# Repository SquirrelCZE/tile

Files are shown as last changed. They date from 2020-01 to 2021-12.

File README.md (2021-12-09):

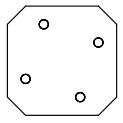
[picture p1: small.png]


# Tile

Tile is a generic mounting system designed for small robots. 
It is a specification of dimensions of one mount position with positions of four screws.
The idea is that one can attach anything to said position, from 3D printed parts to PCBs.

This gives as abillity to easily reuse parts and rebuild the robot in different configuration easily, same way one could expect from LEGO.
The key difference is that it is more sturdy (as screws are used) and it is easy to make compatible PCB.

We intentially designed the tile to allow mounting of parts on thin wall from both sides.
This is achieved by shifting the holes in a way, that when the shape is flipped, the holes won't collide (even when one uses nuts to screw something in place)

The position is shaped like square with beveled corners, this makes it possible to form a grid of mount positions. 
Bigger parts can overlap multiple tiles, it is up to designed to decided whenever that is sensible choice.
Corners are beveled to create a spot between positions on grid for wires.

Given that we use this for 3D printing, the models expect nuts to be inserted in the models to get proper screw thread.

The most used configuration T24 is 24x24mm square with four positions for M2 screws.

The tile is used in our robot Koke heavily https://schpin.org/robots/koke.html and we allready benefited from this on another robot that just reused a lot of the parts.

## Repository content

The main truth for the tile is it's SCAD library - `tile.scad`.
The rest of the repository is as follows:

 * **dxf/** contains dxf shapes for some grid layous that can be directly imported to other CADs made with SCAD. Note that SCAD approximates circles with n-gon.	
 * **example/** simple examples of tile shapes that can be used
 * **extra/** contains more complex models using tile, such as holder for raspberry or 90degree bracket.
 * **pcb/** PCBs used for our robot designed in KiCAD that are Tile compatible.

## Gallery

### Examples

Simple square with T24 mount on both sides:

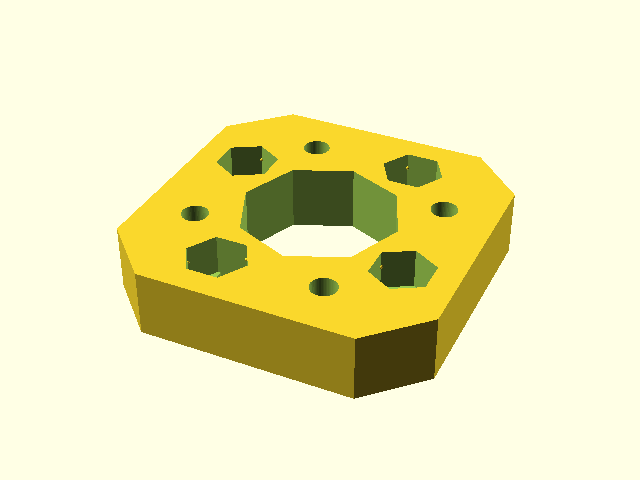
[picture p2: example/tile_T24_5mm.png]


### Koke

This is an example of more complex assembly: part of Koke's leg.
You can see that the parts are connected with tiles (such as the tip of the leg) and that there are multiple tile mount spots.

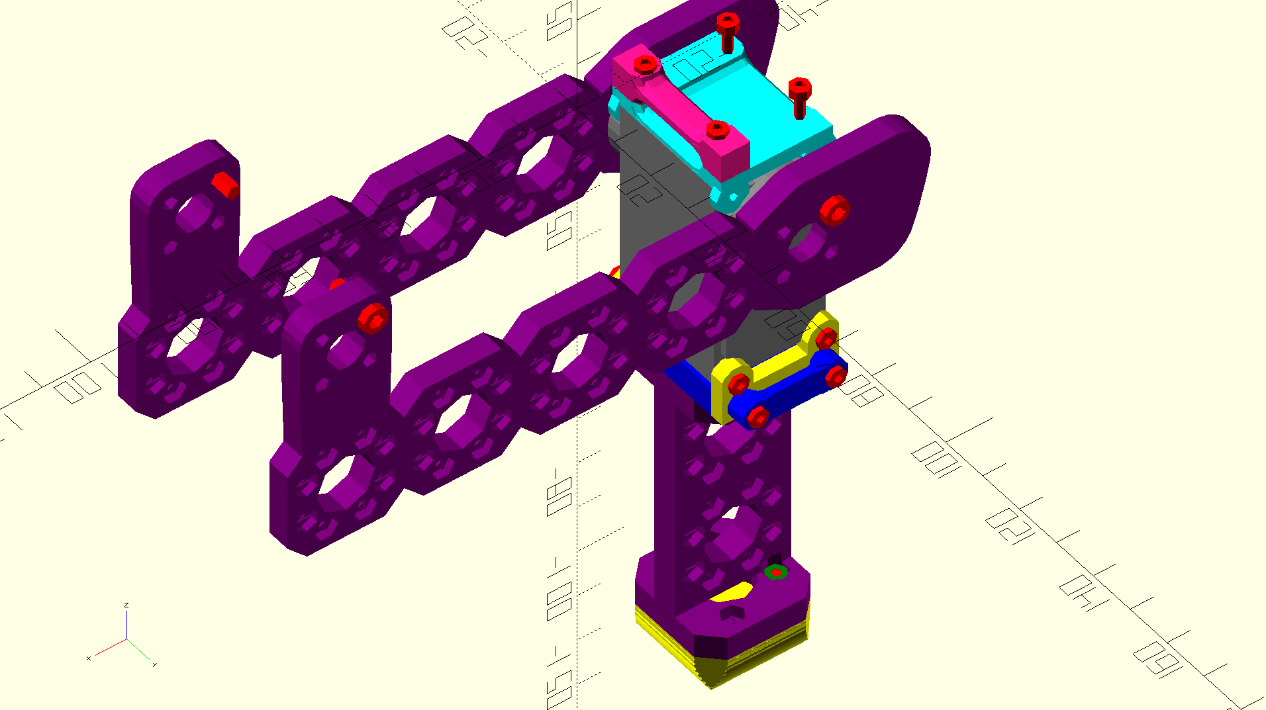
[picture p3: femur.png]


### PCBs

There are two PCBs that are in production stage (that is they may be improved in time but there is little motivation to do so). 
Both are designed in KiCAD and we buy them in bulk.

The first one is small 4-layer power distribution board for use with our servomotors.
The power is brought in usually via the XT30 connector space and we have multiple of these on the robot itself.
We have custom footprint for servoconnectors that is compatible with servomotor connectors with 2.54/2mm spacing with pins in following configuration: S|VCC|GND. 
The idea is that servomotors are connected to free servo connectors and one is left to connect the S| |GND pair to the controller (that is, without the VCC line).

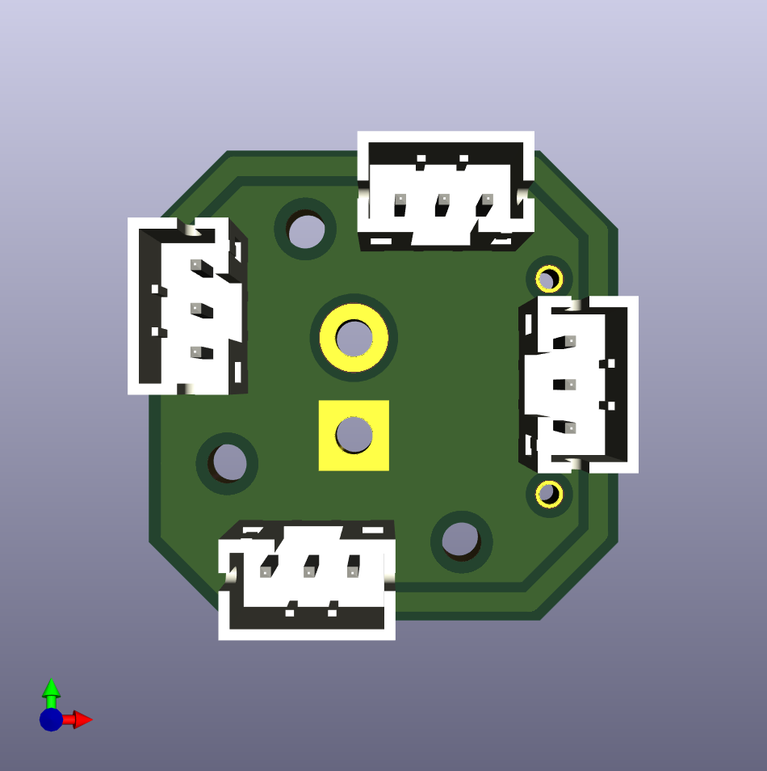
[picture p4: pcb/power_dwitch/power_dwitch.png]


Second board is just really simple holder for two housings for 18650 batteries, that are pararelly connected. 
There are no connectros to be used, rather we expect the wires to be soldered directly on the board itself.

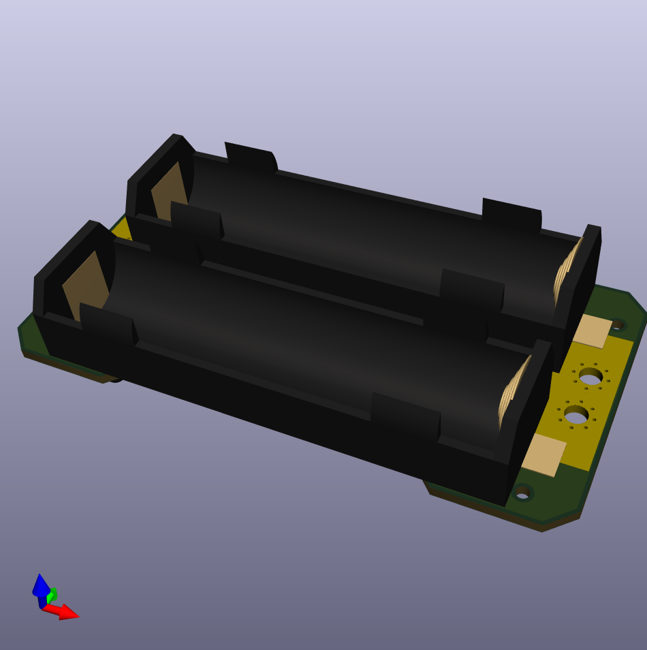
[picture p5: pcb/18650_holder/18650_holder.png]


### Prototype PCBs

We have a prototype of board with STM32G4 processor that can be powered from PDB board above.
The board is designed to control our servomotors or to be attached to same communication bus.

The v1 prototype worked (as we could write code for it and blink a LED), but it misses logic level shifter for the servo bus which makes it not really usable.

The v2 fixes that and even adds IMU, however we should switch to smaller package for the processor to fit all on one side of the PCB and we can't do that now given chip shortage, so v2 is delayed until we can do that.

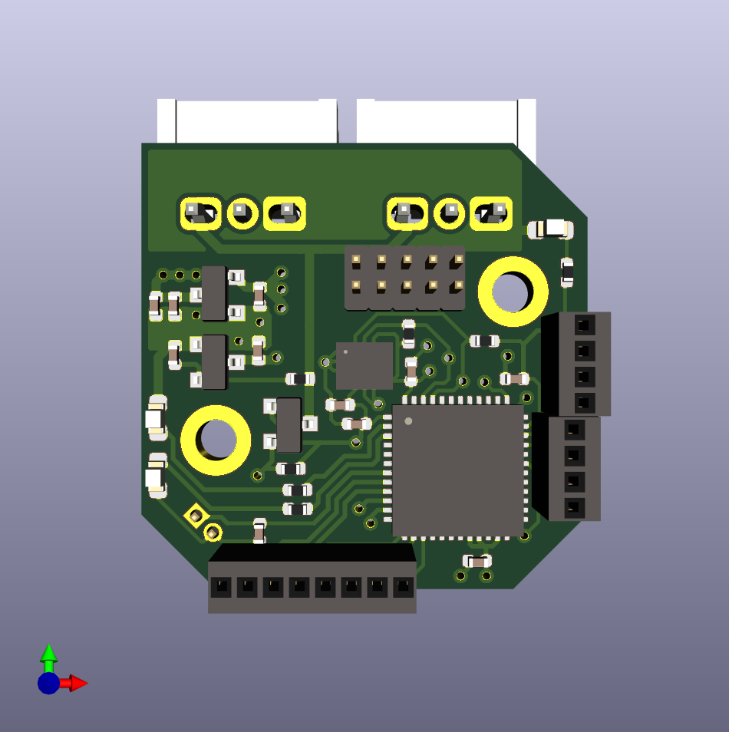
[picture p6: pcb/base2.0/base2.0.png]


## Drawings of T24

All dimensions are in `mm`.

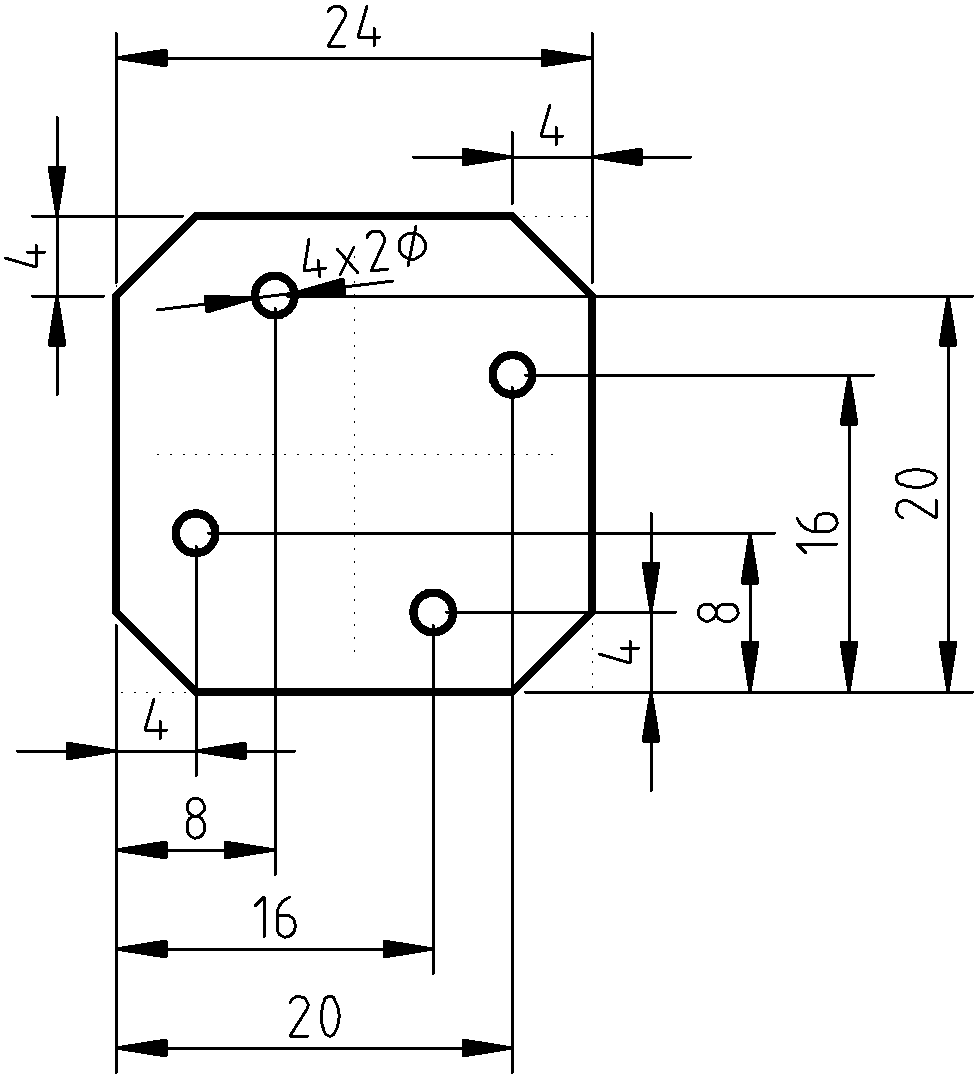
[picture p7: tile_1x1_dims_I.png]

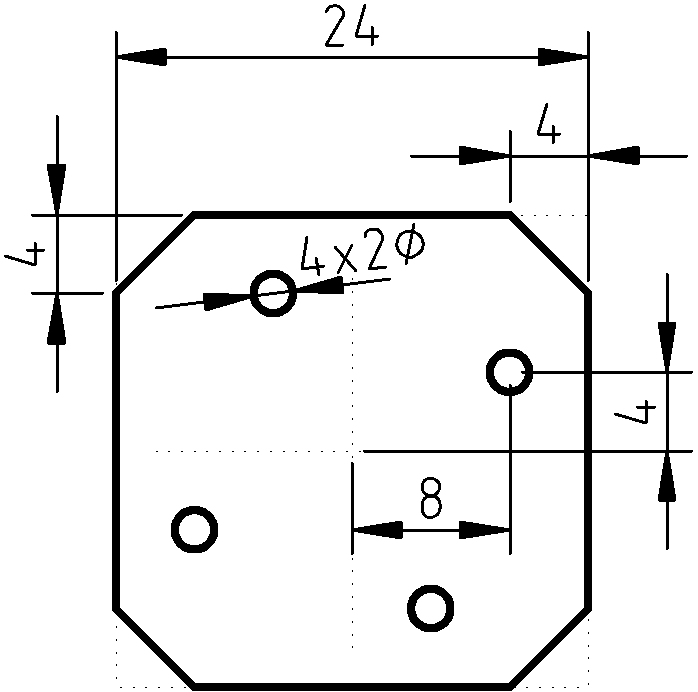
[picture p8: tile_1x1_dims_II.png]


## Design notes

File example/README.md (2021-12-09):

# Gallery of tile examples
## example/tile_T24_5mm_centered.scad
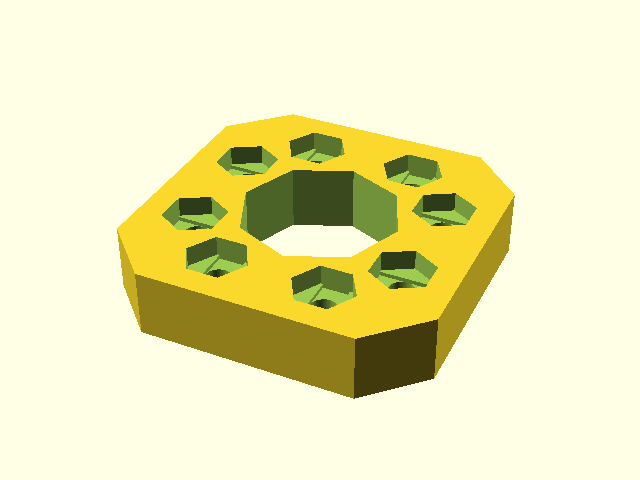
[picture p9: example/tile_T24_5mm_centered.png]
example/tile_T24_5mm_centered

## example/tile_H_T24_5mm.scad
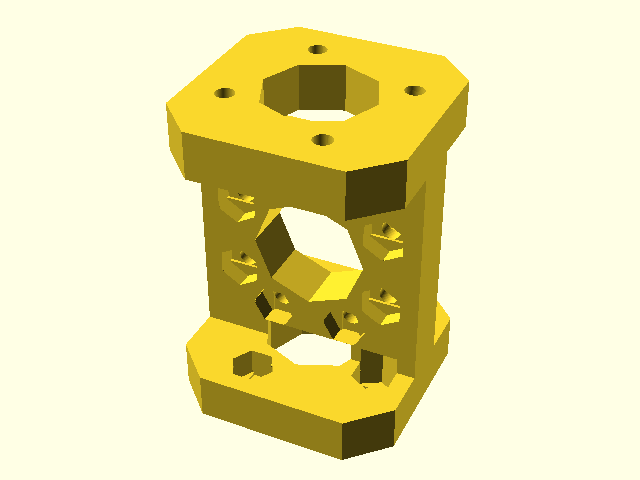
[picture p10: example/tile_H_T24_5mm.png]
example/tile_H_T24_5mm

## example/tile_sandwitch.scad
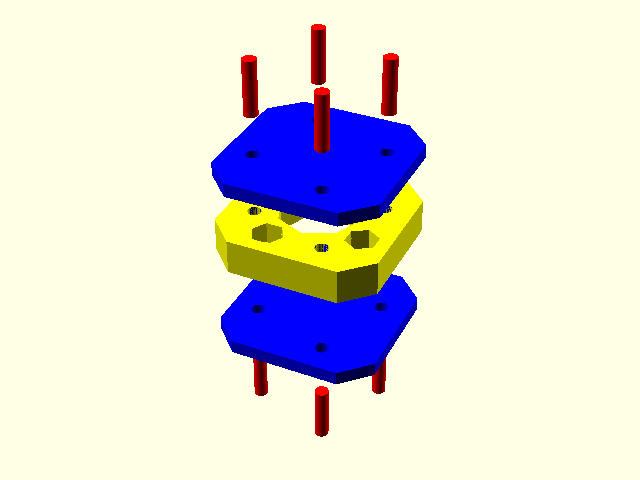
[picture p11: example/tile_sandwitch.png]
example/tile_sandwitch

## example/tile_T24_2mm.scad
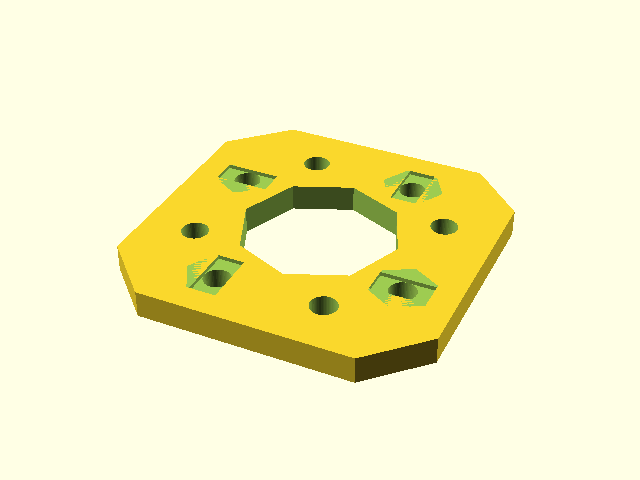
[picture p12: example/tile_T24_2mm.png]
example/tile_T24_2mm

## example/tile_raw_plate_T24_2x3_2mm.scad
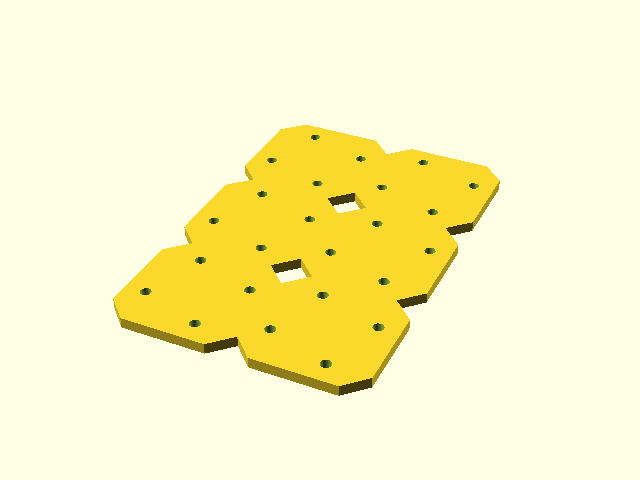
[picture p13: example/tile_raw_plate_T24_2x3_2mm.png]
example/tile_raw_plate_T24_2x3_2mm

## example/tile_T36_5mm.scad
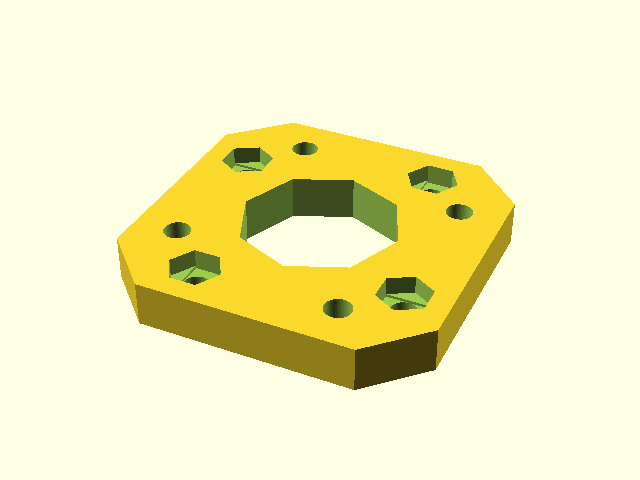
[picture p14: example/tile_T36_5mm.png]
example/tile_T36_5mm

## example/tile_T24_5mm.scad
example/tile_T24_5mm

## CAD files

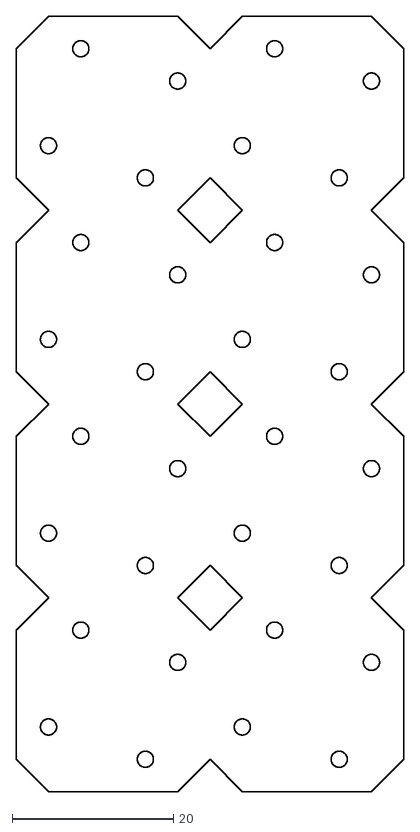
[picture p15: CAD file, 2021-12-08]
dxf/tile_2x4.dxf
48.0 x 96.0

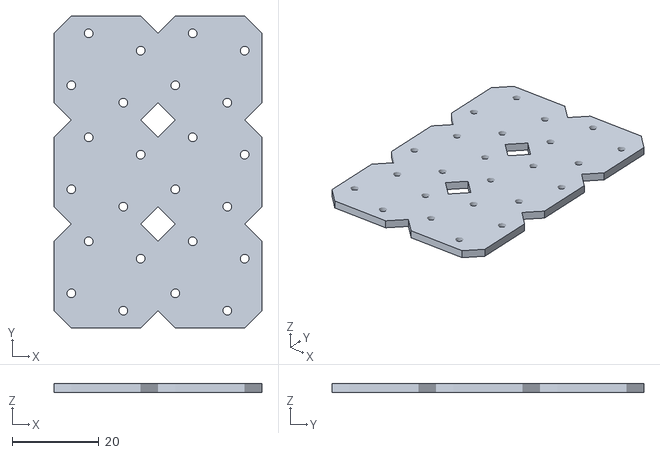
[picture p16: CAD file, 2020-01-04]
example/tile_raw_plate_T24_2x3_2mm.stl
48.0 x 72.0 x 2.00

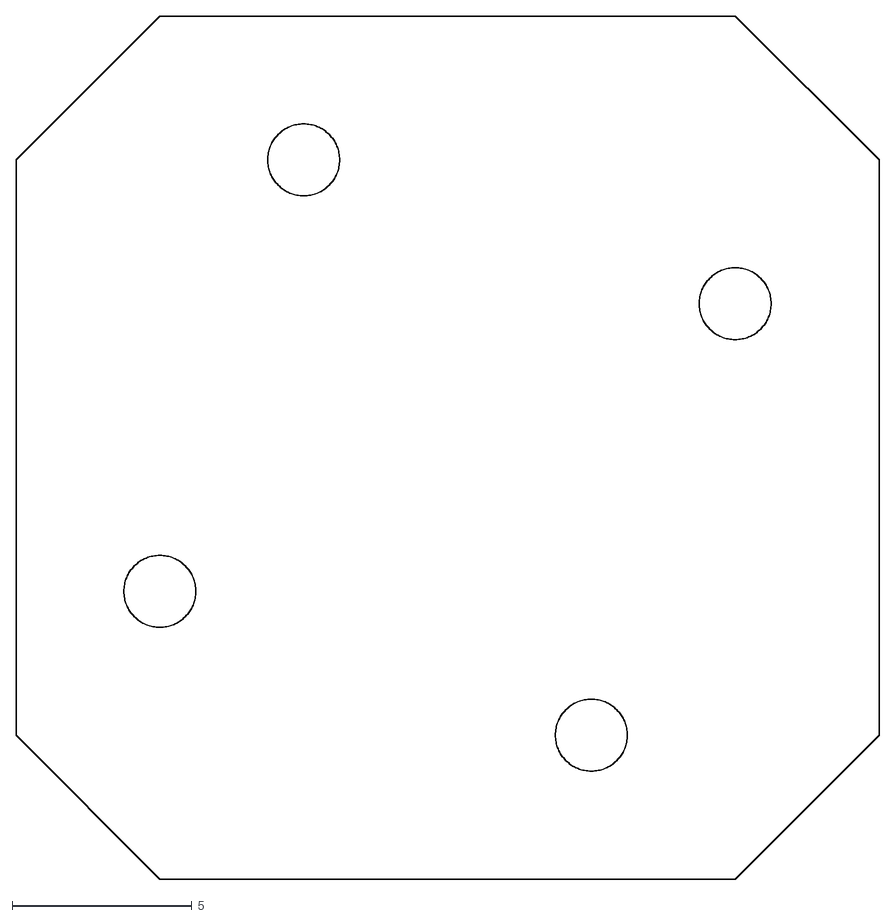
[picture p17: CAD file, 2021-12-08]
dxf/tile_1x1.dxf
24.0 x 24.0

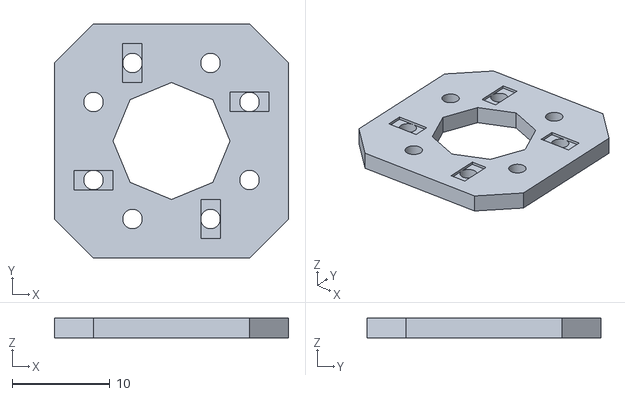
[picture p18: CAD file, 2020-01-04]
example/tile_T24_2mm.stl
24.0 x 24.0 x 2.00

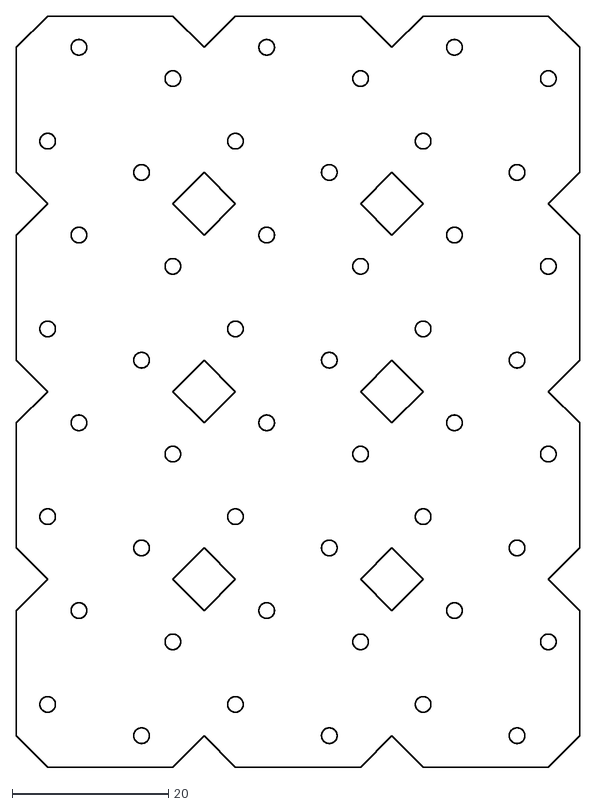
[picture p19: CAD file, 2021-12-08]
dxf/tile_3x4.dxf
72.0 x 96.0

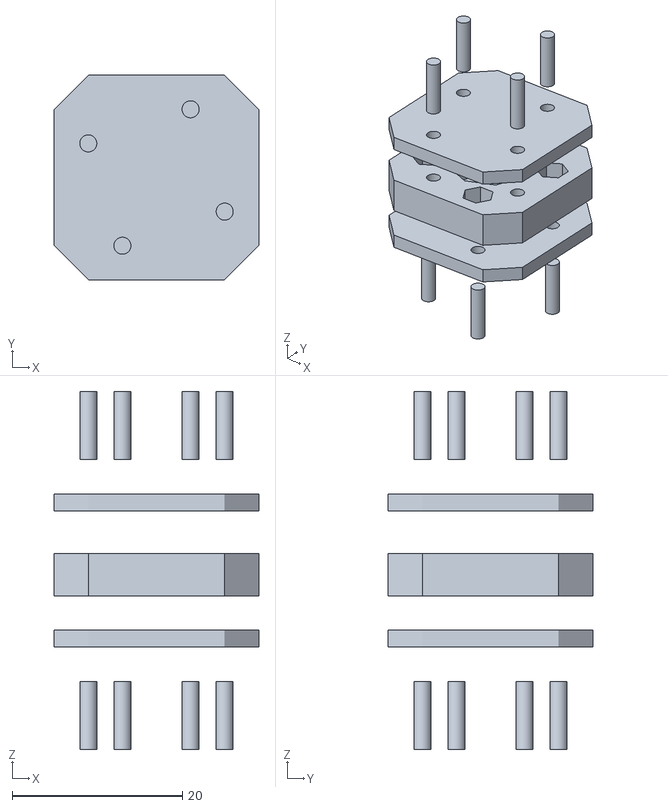
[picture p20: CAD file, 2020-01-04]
example/tile_sandwitch.stl
24.0 x 24.0 x 42.0

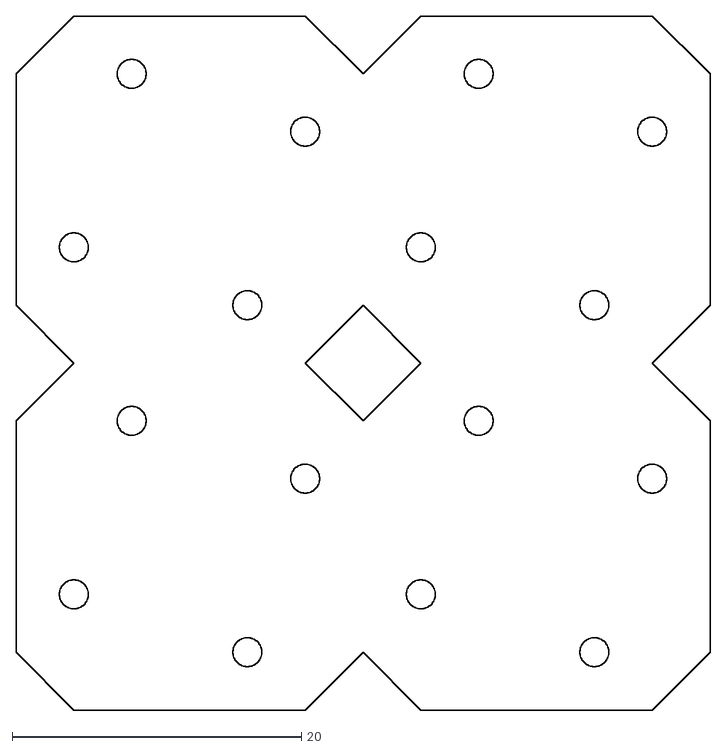
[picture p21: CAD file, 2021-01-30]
dxf/tile_2x2.dxf
48.0 x 48.0

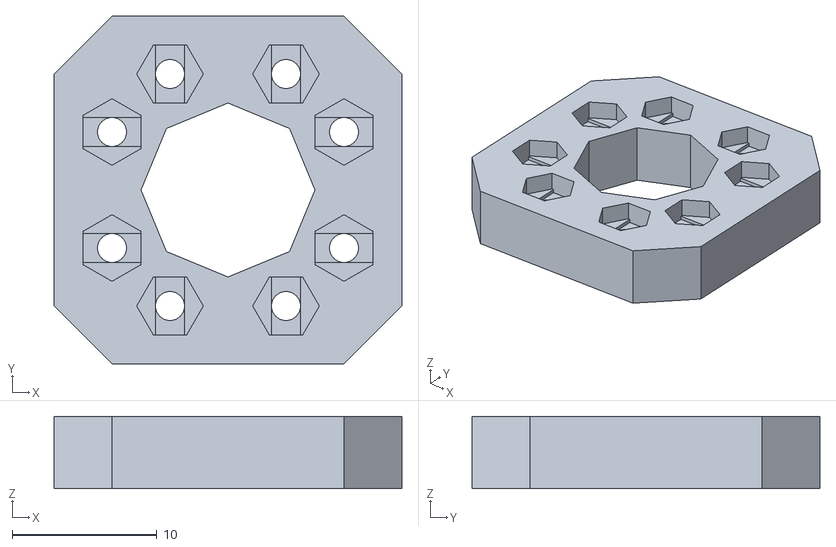
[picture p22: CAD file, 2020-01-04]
example/tile_T24_5mm_centered.stl
24.0 x 24.0 x 5.00

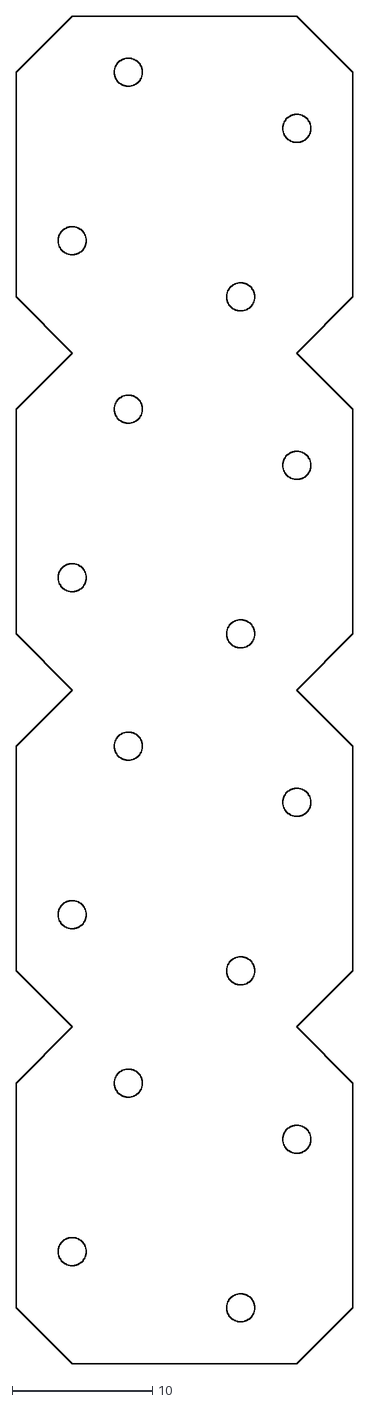
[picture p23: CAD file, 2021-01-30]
dxf/tile_1x4.dxf
24.0 x 96.0

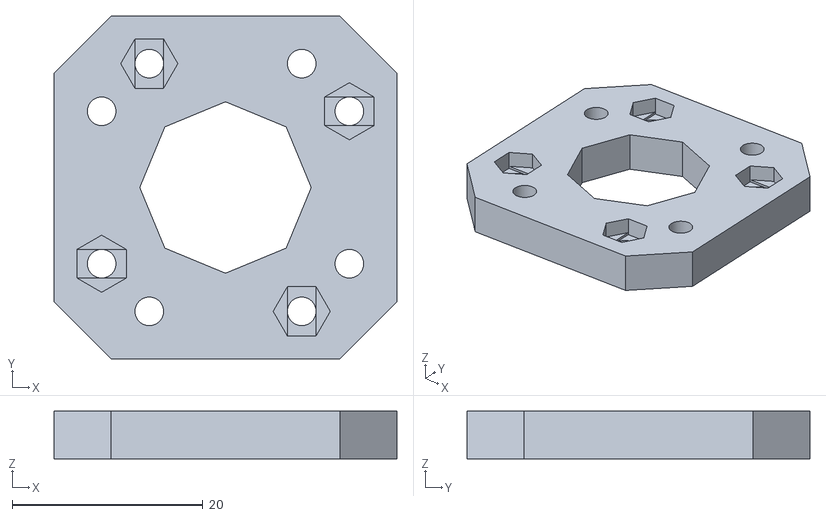
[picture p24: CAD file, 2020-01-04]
example/tile_T36_5mm.stl
36.0 x 36.0 x 5.00

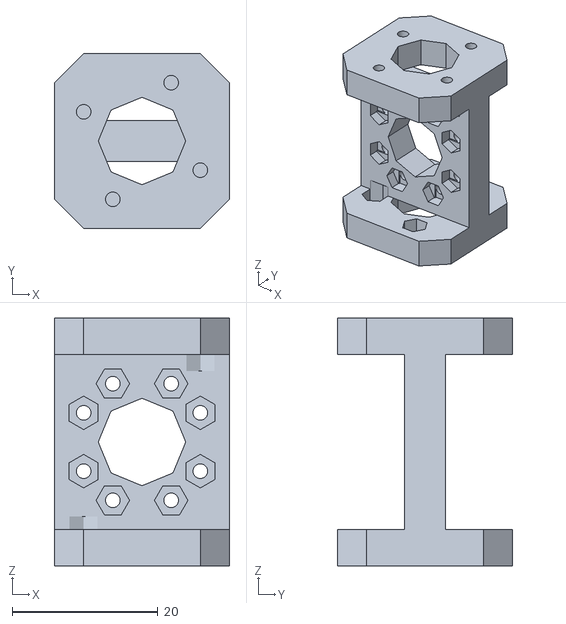
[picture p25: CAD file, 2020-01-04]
example/tile_H_T24_5mm.stl
24.0 x 24.0 x 34.0

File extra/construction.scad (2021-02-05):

include<../tile.scad>;

t = 2;

$fn = 64;
// for (i = [ -1, 0, 1 ]) translate([ i * Ta(T24), 0, 0 ]) tile(T24, 4);

module bracket_base() difference() {
  union() {
    for (rot = [ [ 0, 90, 0 ], [ 180, 0, 0 ] ])
      rotate(rot) translate([ Ta(T24) / 2, 0, 0 ]) tile_raw_plate(T24, 1, 1, 4);
  }

  for (rot = [ [ 0, 90, 0 ], [ 180, 0, 0 ] ])
    rotate(rot) translate([ Ta(T24) / 2, 0, 0 ]) {
      tile_center_hole(T24, h = 100, center = true);
      tile_screw_pos(T24){
	  cylinder(d = Tscrew_d(T24), h = 100, center = true);
		translate([0,0,t])
		cylinder(d= Tnut_d(T24), h=Ta(T24)/2 - t, $fn=6);
		}
    }
}

module bracket_support(i) {
  hull() intersection() {
    bracket_base();
    translate([ 0, i * Ta(T24), 0 ]) cube([ 100, t, 100 ], center = true);
  }
}

module bracket() {
  bracket_base();
  for (i = [ -0.5, 0.5 ]) difference() {
      bracket_support(i);
      scale([ 0.7, 1, 0.7 ]) bracket_support(i);
    }
}

bracket();

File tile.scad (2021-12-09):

//      0   1             2         3  4      5      6
//    [ a,  screw_coord,  corner_r, t, nut_d, nut_h, screw_d]
T36 = [ 36, [ 13, 8, 0 ], 6.000000, 3, 6.000, 2.500, 3 ];
T24 = [ 24, [ 08, 4, 0 ], 4.000000, 2, 4.750, 1.800, 2 ];

tile_k = 0.07;

function Ta(class) = class[0];
function Tscrew_coord(class) = class[1];
function Tcorner(class) = class[2];
function Tt(class) = class[3];
function Tnut_d(class) = class[4];
function Tnut_h(class) = class[5];
function Tscrew_d(class) = class[6];

module tile(class = T24, h = 5, center = false, centered_hole = false) difference() {
	tile_pos(class = class, h = h, center = center);
	tile_neg(class = class, h = h, center = center,
		 centered_hole = centered_hole);
}

module tile_neg(class, h, center = false, centered_hole = false) {
	translate([ 0, 0, center ? 0 : h / 2 ]) for (alpha = [ 0, 180 ])
	    rotate([ alpha, 0, 0 ]) tile_screw_pos(class = class)
		tile_screw_hole(class = class, h = h,
				centered_hole = centered_hole);
	tile_center_hole(class, h + 2, center = center);
}

module tile_pos(class, h, center = false)
    linear_extrude(height = h, center = center, convexity = 10)
	tile_relief(class = class);

module tile_H(class = T24, h = 5, n = 1, center_t = undef) render()
    difference() {
	top_offset = n * Ta(class) + h;
	z_center = n * Ta(class) / 2 + h;
	center_t =
	    (center_t == undef) ? Tt(class) + 2 * Tnut_h(class) : center_t;

	union() {
		translate([ 0, 0, z_center ])
		    cube([ Ta(class), center_t, n * Ta(class) + 2 * h ],
			 center = true);
		for (z = [ 0, top_offset ])
			translate([ 0, 0, z ]) linear_extrude(height = h)
			    tile_base_shape(l = Ta(class),
					    corner_r = Tcorner(class));
	}

	for (i = [0.5:n])
		translate([ 0, 0, h + i * Ta(class) ]) rotate([ 90, 0, 0 ]) {
			tile_neg(class, h = center_t, center = true,
				 centered_hole = true);
			tile_center_hole(class, h = center_t, center = true);
		}

	for (z = [ 0, top_offset ])
		translate([ 0, 0, z ]) tile_center_hole(class, h = h);

  mirror([0,0,1])
      mirror([ 1, 0, 0 ]) tile_screw_pos(class = class)
	    translate([ 0, 0, -h / 2 ]) tile_screw_hole(class = class, h = h);

	tile_screw_pos(class = class)
	    translate([ 0, 0, top_offset + Tt(class) ])
		tile_screw_hole(class = class, h = h);
}

module tile_box_side_pos() {
	children();
	for (alpha = [0:90:360]) rotate([ 90, 0, alpha ]) children();
	rotate([ 180, 0, 0 ]) children();
}

module tile_box(class) difference() {
	hull() {
		r = Tt(class);
		cube([ Ta(class) - r, Ta(class) - r, Ta(class) ],
		     center = true);
		cube([ Ta(class), Ta(class) - r, Ta(class) - r ],
		     center = true);
		cube([ Ta(class) - r, Ta(class), Ta(class) - r ],
		     center = true);
	}

	tile_box_side_pos() cylinder(d = Ta(class) / 2, h = Ta(class));

	tile_box_side_pos() tile_screw_pos(class = class)
	    translate([ 0, 0, Ta(class) / 2 - Tnut_h(class) - 1.5 * Tt(class) ])
		Mnut_sidehole(M2N, 10);
	tile_box_side_pos() tile_screw_pos(class = class)
	    cylinder(d = Tscrew_d(class), h = 20);
}

module tile_raw_plate(class, x, y, t) {
	for (i = [0:x - 1])
		for (j = [0:y - 1])
			translate([ i * Ta(class), j * Ta(class), 0 ])
			    difference() {
				tile_pos(class, h = t, center = false);
				tile_screw_pos(class = class)
				    cylinder(d = Tscrew_d(class), h = 100,
					     center = true);
			}
}

//          Implementation
// ------------------------------------

module tile_center_hole(class, h, center = false) {
  translate([ 0, 0, - tile_k ])
	  cylinder(d = Ta(class) / 2, h = h + 2, center = center, $fn = 8);
}

module tile_base_shape(l, corner_r) {
	hull() {
		square([ l - corner_r * 2, l ], center = true);
		square([ l, l - corner_r * 2 ], center = true);
	}
}

module tile_relief(class, a, corner_r, t, nut_d) {
	tile_base_shape(Ta(class), Tcorner(class));
}

module tile_screw_pos(class) {
	for (alpha = [0:90:360])
		rotate([ 0, 0, alpha ]) translate(Tscrew_coord(class))
		    children();
}

module tile_plate(class, t) difference() {
	linear_extrude(height = t) tile_base_shape(Ta(class), Tcorner(class));

	mirror([ 1, 0, 0 ]) tile_screw_pos(class)
	    cylinder(d = Tscrew_d(class), h = t * 3, center = true);
}

module tile_screw_hole(class, h, centered_hole = false) {
	layer_t = 0.3;
	nut_e = sqrt(pow(Tnut_d(class), 2) - pow(Tnut_d(class) / 2, 2));

	cylinder(d = Tscrew_d(class), h = h + 2, center = true);
	if (centered_hole) {
		for (alpha = [ 0, 180 ])
			rotate([ alpha, 0, 0 ])
			translate([ 0, 0, Tt(class) / 2 ])
				difference() {
					union(){
						cube([ nut_e, Tscrew_d(class), layer_t * 2 ],
				     	center = true);
						rotate([ 0, 0, 30 ])
				    	cylinder(d = Tnut_d(class), h = h, $fn = 6);
					}
					tile_screw_clips(class);
				}
	} else {
		rotate([180,0,0])
		translate([ 0, 0, Tt(class) - h / 2 ]) difference() {
			union() {
				cube([ nut_e, Tscrew_d(class), layer_t * 2 ],
				     center = true);
				rotate([ 0, 0, 30 ])
					cylinder(
				    d = Tnut_d(class),
			  		h = h - Tt(class) + Tnut_h(class), $fn = 6);
			}
			tile_screw_clips(class);
		}
	}
}

module tile_screw_clips(class) {
	for(an=[0, 120, -120])
		rotate([0,0,an+30])
		translate([Tnut_d(class)/2, 0, Tnut_h(class)])
			sphere(r=Tnut_d(class)*0.03);
}

module tile_tube_hole(d) {
	rotate([ 90, 0, 0 ]) cylinder(d = d, h = 100, center = true);
}

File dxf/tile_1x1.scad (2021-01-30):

include <../tile.scad>

projection()
tile_raw_plate(T24, 1, 1, 2);

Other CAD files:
example/tile_T24_5mm.stl
dxf/tile_1x4.scad
dxf/tile_2x2.scad
dxf/tile_2x4.scad
dxf/tile_3x4.scad
example/tile_H_T24_5mm.scad
example/tile_T24_2mm.scad
example/tile_T24_5mm.scad
example/tile_T24_5mm_centered.scad
example/tile_T36_5mm.scad
example/tile_raw_plate_T24_2x3_2mm.scad
example/tile_sandwitch.scad
extra/realsense.scad
extra/rpi.scad

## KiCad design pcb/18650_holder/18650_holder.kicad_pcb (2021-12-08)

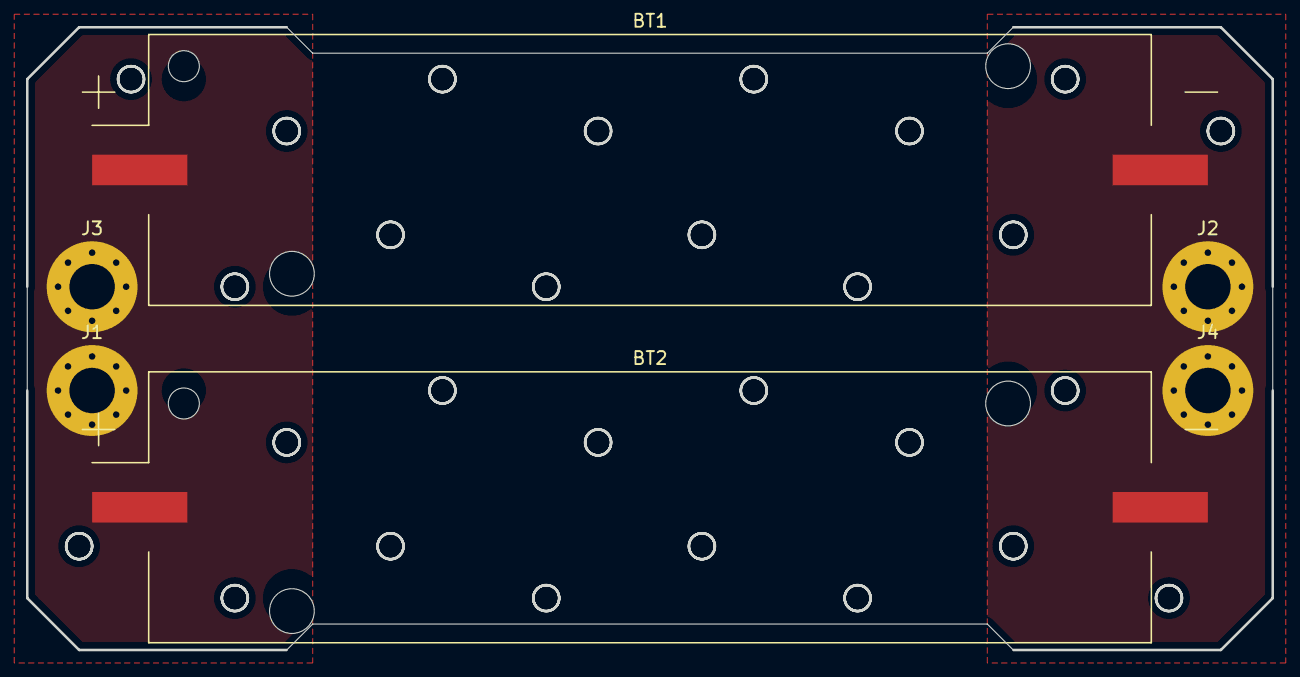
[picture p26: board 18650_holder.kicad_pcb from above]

Board: 2 copper layers, 96.0 x 48.0 mm, 6 parts (0 on the bottom side), 2 nets, no tracks yet.

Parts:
BT1, BT2: Battery_Cell; 18650_holder
J1, J2, J3, J4: Conn_01x01_Male; MountingHole_3.5mm_Pad_Via

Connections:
GND: BT1.2, BT2.2, J2.1, J4.1
VCC: BT1.1, BT2.1, J1.1, J3.1

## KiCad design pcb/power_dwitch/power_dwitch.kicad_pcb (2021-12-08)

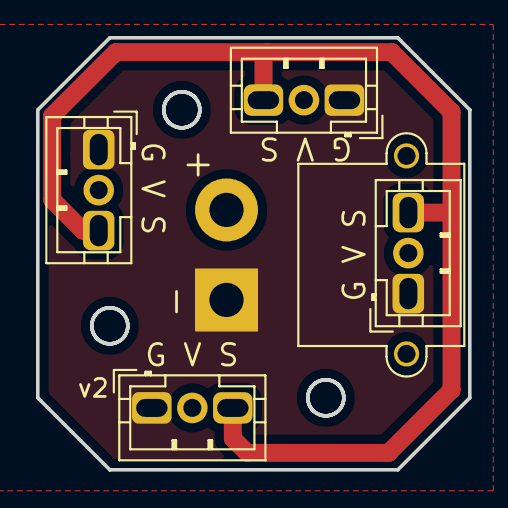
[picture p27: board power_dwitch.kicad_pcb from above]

Board: 4 copper layers, 24.0 x 24.0 mm, 5 parts (0 on the bottom side), 3 nets.

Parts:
J1, J2, J3, J4: Conn_01x03_Male; JST_PH_B3B-PH-K_1x03_P2.00mm_Vertical
J5: Conn_01x02_Male; AMASS_XT30PW-M_1x02_P2.50mm_Horizontal

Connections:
GND: J1.1, J2.1, J3.1, J4.1, J5.1
S: J1.3, J2.3, J3.3, J4.3
VCC: J1.2, J2.2, J3.2, J4.2, J5.2

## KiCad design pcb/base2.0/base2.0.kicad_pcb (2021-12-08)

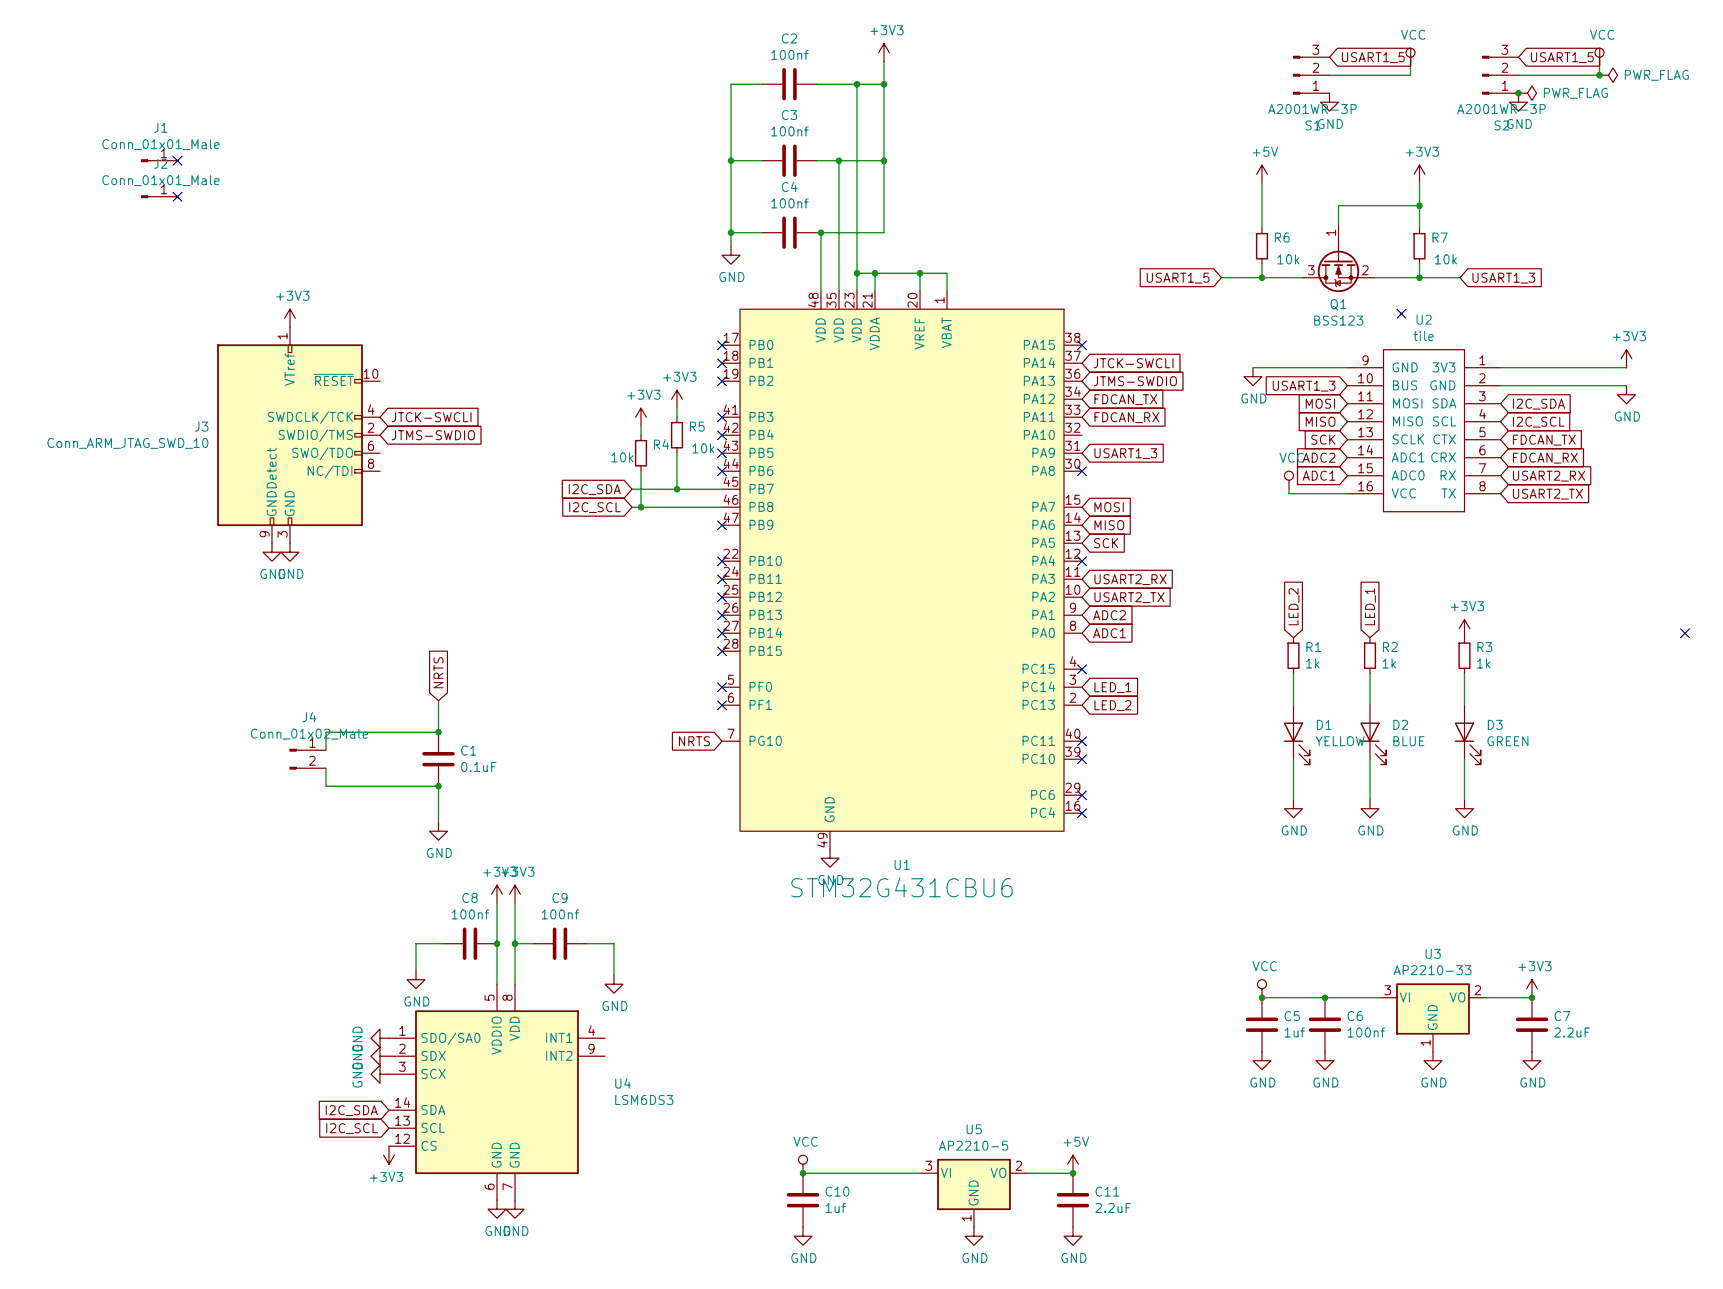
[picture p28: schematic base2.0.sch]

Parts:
C1: 0.1uF; C_0402_1005Metric; LCSC C1525
C2, C3, C4, C6, C8, C9: 100nf; C_0402_1005Metric; LCSC C1525
C5, C10: 1uf; C_0402_1005Metric; LCSC C52923
C7, C11: 2.2uF; C_0402_1005Metric; LCSC C12530
D1: YELLOW; LED_0603_1608Metric; LCSC C72038
D2: BLUE; LED_0603_1608Metric; LCSC C72041
D3: GREEN; LED_0603_1608Metric; LCSC C72043
J1, J2: Conn_01x01_Male; MountingHole_2.2mm_M2_DIN965_Pad
J3: Conn_ARM_JTAG_SWD_10; PinHeader_2x05_P1.27mm_Vertical
J4: Conn_01x02_Male; PinHeader_1x02_P1.27mm_Vertical
Q1: BSS123; SOT-23
R1, R2, R3: 1k; R_0402_1005Metric; LCSC C11702
R4, R5, R6, R7: 10k; R_0402_1005Metric; LCSC C25744
S1, S2: A2001WR-3P; jst_bus_horizontal
U1: STM32G431CBU6; QFN-48-1EP_7x7mm_P0.5mm_EP5.6x5.6mm; LCSC C529356
U2: tile
U3: AP2210-33; SOT-23; LCSC C155508
U4: LSM6DS3; LGA-14_3x2.5mm_P0.5mm_LayoutBorder3x4y
U5: AP2210-5; SOT-23; LCSC C500758

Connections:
+3V3: C2.1, C3.1, C4.1, C7.1, C8.1, C9.2, J3.1 (VTref), Q1.1 (G), R3.1, R4.1, R5.1, R7.1, U1.1 (VBAT), U1.20 (VREF), U1.21 (VDDA), U1.23 (VDD), U1.35 (VDD), U1.48 (VDD), U2.1 (3V3), U3.2 (VO), U4.5 (VDDIO), U4.8 (VDD), U4.12 (CS)
+5V: C11.1, R6.1, U5.2 (VO)
ADC1: U1.8 (PA0), U2.15 (ADC0)
ADC2: U1.9 (PA1), U2.14 (ADC1)
FDCAN_RX: U1.33 (PA11), U2.6 (CRX)
FDCAN_TX: U1.34 (PA12), U2.5 (CTX)
GND: C1.2, C2.2, C3.2, C4.2, C5.2, C6.2, C7.2, C8.2, C9.1, C10.2, C11.2, D1.1 (K), D2.1 (K), D3.1 (K), J3.3 (GND), J3.5 (GND), J3.9 (GNDDetect), J4.2, S1.1, S2.1, U1.49 (GND), U2.2 (GND), U2.9 (GND), U3.1 (GND), U4.1 (SDO/SA0), U4.2 (SDX), U4.3 (SCX), U4.6 (GND), U4.7 (GND), U5.1 (GND)
I2C_SCL: R4.2, U1.46 (PB8), U2.4 (SCL), U4.13 (SCL)
I2C_SDA: R5.2, U1.45 (PB7), U2.3 (SDA), U4.14 (SDA)
JTCK-SWCLI: J3.4 (SWDCLK/TCK), U1.37 (PA14)
JTMS-SWDIO: J3.2 (SWDIO/TMS), U1.36 (PA13)
LED_1: R2.1, U1.3 (PC14)
LED_2: R1.1, U1.2 (PC13)
MISO: U1.14 (PA6), U2.12 (MISO)
MOSI: U1.15 (PA7), U2.11 (MOSI)
NRTS: C1.1, J4.1, U1.7 (PG10)
unnamed: D1.2 (A), R1.2
unnamed: D2.2 (A), R2.2
unnamed: D3.2 (A), R3.2
SCK: U1.13 (PA5), U2.13 (SCLK)
USART1_3: Q1.2 (S), R7.2, U1.31 (PA9), U2.10 (BUS)
USART1_5: Q1.3 (D), R6.2, S1.3, S2.3
USART2_RX: U1.11 (PA3), U2.7 (RX)
USART2_TX: U1.10 (PA2), U2.8 (TX)
VCC: C5.1, C6.1, C10.1, S1.2, S2.2, U2.16 (VCC), U3.3 (VI), U5.3 (VI)

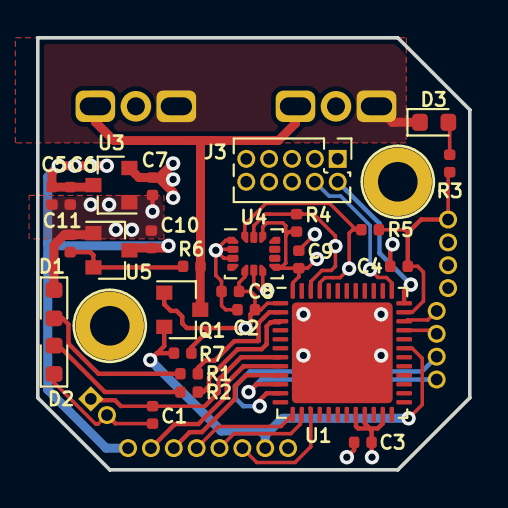
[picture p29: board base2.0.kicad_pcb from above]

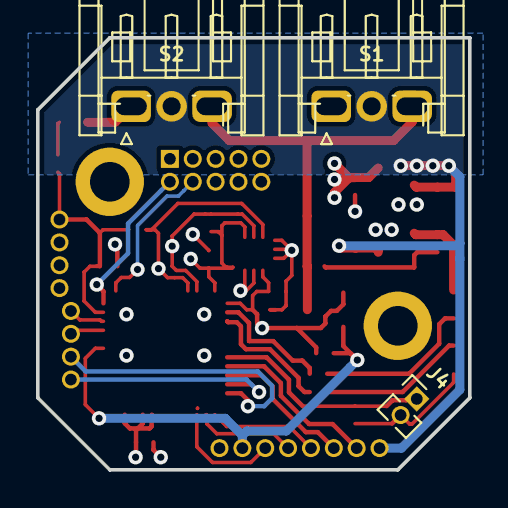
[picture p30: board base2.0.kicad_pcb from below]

Board: 4 copper layers, 24.0 x 24.0 mm, 33 parts (3 on the bottom side), 25 nets.

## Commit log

2020-01-04 added tile.scad examples
    [example.scad, tile.scad, tile_H_T24_5mm.scad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]
2020-01-04 updated tile_H example
    [tile_H_T24_5mm.scad, tile_H_T24_5mm.stl]
2020-01-04 added sandwitch example
    [tile_sandwitch.scad, tile_sandwitch.stl]
2020-01-04 fixed rendering resolution and added shape png
    [dxf.scad, tile_H_T24_5mm.stl, tile_T24_2mm.stl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]
2020-12-11 added puncholes dxf
    [punchholes.dxf]
2021-01-30 cleaning/upgrades got collection of little modes over sime time, added dxf"
    [#tile_1x1.dxf, base.kicad_pcb, base.sch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]
2021-01-30 fixed holes orientation
    [example.scad, tile.scad]
2021-01-30 fixed tile_H
    [tile.scad]
2021-02-05 added scad
    [construction.scad, realsense.scad, rpi.scad]
2021-02-19 fixed errors in scheme
    [base2.0.sch]
2021-07-14 le update
    [base2.0.kicad_pcb, base2.0.sch]
2021-09-10 Small changes to base pcb
    [base2.0.kicad_pcb, base2.0.sch]
2021-09-10 fixed i2c lines on base2.0 pcb
    [base2.0.kicad_pcb]
2021-11-21 removed base output files
    [base2.0-CmtUser.gbr, base2.0-CuBottom.gbr, base2.0-CuTop.gbr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]
2021-12-08 added another pcbs
    [#tile_1x1.dxf, 18650_holder.kicad_pcb, 18650_holder.sch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]
2021-12-08 added pics of pcbs
2021-12-08 added pics of pcbs to readme
2021-12-09 Modified sandwitch example
    [tile_sandwitch.scad]
2021-12-09 Added default params, clips and increase M2 nut size
    [tile.scad]
